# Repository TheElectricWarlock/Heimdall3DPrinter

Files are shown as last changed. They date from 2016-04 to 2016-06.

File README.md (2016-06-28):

# Heimdall3DPrinter
The Heimdall is a CoreXY 3D Printer capable of fast and reliable printing. It uses 1515 Aluminum extrusions for the enclosing frame. 

For more information regarding the printer visit the project's wiki.

## Changelog

### Version 1.3

-Improvements in XY stepper motor brackets for better stability.

### Version 1.2

-Added two new types of clips for better cable management that insert on the 1515 extrusions. 

### Version 1.1

-Added a new 1515 Extrusion to the back of the frame for mounting the power supply, Arduino Mega and Ramps.
-New Brackets for the power supply.
-New Bracket for the Arduino Mega and Ramps board. 
-Changes in bill of materials. 

## Things To Change

-Z Axis and Bed brackets for smoother Z axis movements, bed leveling and stability.

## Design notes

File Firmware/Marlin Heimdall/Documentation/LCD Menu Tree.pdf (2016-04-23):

# Marlin LCD Menu Tree

Main Menu | Tune Menu | Move Menu
Info screen | Main | Prepare
Tune | Speed | Move 10mm | Move Menu
Prepare | Nozzle | Move 1mm | Move axis
Control | Nozzle2 | Move 0.1mm | Move X
Pause print | Nozzle3 | | Move Y
Resume print | Bed | | Move Z
Stop print | Fan speed | Temperature Menu | Extruder
Print from SD | Flow | Control
Change SD card | Babystep X | Nozzle
No SD card | Babystep Y | Nozzle2
Init. SD card | Babystep Z | Nozzle3
| Change filament | Bed
| | Fan speed
| | Autotemp
| Prepare Menu | \002 Min
| Main | \002 Max | Preheat PLA
| Autostart | \002 Fact | Temperature
| Disable steppers | PID-P | Fan speed
| Auto home | PID-I | Nozzle
| Preheat PLA | PID-D | Bed
| Preheat ABS | PID-C | Store memory
| Cooldown | Preheat PLA conf
| Switch power off | Preheat ABS conf | Preheat ABS
Switch power on | Temperature
Move axis | Fan speed
| Motion Menu | Nozzle
| Control | Bed
Control Menu | Z Offset | Store memory
Main | Accel
Temperature | Vxy-jerk
Motion | Vz-jerk
LCD contrast | Ve-jerk
Retract | Vmax x
Store memory | Vmax y
Load memory | Vmax z
Restore failsafe | Vmax e
| Vmin
| VTrav min
SD Card Menu | Amax x
Main | Amax y
Refresh | Amax z
filenames | Amax e
| A-retract
| Xsteps/mm
| Ysteps/mm
| Zsteps/mm
| Esteps/mm
| Endstop abort

Retract Menu
Control
AutoRetr.
Retract mm
Retract F
Hop mm
UnRet +mm
UnRet F

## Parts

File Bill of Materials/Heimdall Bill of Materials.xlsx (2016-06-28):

Item # | Item Name | Amount | Source/Where to buy | Comment
Electronics
1 | Arduino Mega | 1 | Folgertech or Ebay. | Cheap Chinese copies should work well too.
2 | Ramps Shield | 1 | Folgertech or Ebay. | Cheap Chinese copies should work well too.
3 | Polulu Stepper Drivers | 4 | Folgertech or Ebay. | You can buy at least 1 more than the number shown here, just in case you fry one.
4 | Nema 17 Stepper Motors | 4 | Folgertech or Ebay. | The bigger the better, mostly for the Extruder.
5 | Makerbot Style Endstops | 3 | Folgertech or Ebay. | Simple endstops can be found anywhere.
6 | 360W 12V Power Supply | 1 | Folgertech or Ebay. | You can buy a lower watage one if not using a heated bed.
7 | Heated bed (200x200mm) | 1 | Folgertech or Ebay. | Optional, you can still use the printer without one. You get more printing area, but might not be able to print with abs.
8 | Hotend w/ Fan | 1 | E3D, Folgertech or Ebay. | You can buy your hotend wherever you want, as long as it is not too cheap and is similar to an E3D.
Mechanical Parts
9 | 5/16 - 18 Stainless Steel Threaded Rod (340mm) | 1 | Home Depot or any hardware store. | Z axis Threaded rod, if you want to use a Metric one, you can use a M8 Stainless Steel threaded rod.
10 | 5/16 - 18 Stainless Steel Nuts | 3 | Home Depot or any hardware store. | You only need one, more just in case. For Metric, you can use an M8 nut.
11 | 8mm Hardened Linear Rods X (260mm) | 2 | Folgertech or Ebay. | If the seller does not have this size, you might need to order a slightly longer one and cut it yourself.
12 | 8mm Hardened Linear Rods Y (390mm) | 2 | Folgertech or Ebay. | If the seller does not have this size, you might need to order a slightly longer one and cut it yourself.
13 | 8mm Hardened Linear Rods Z (400mm) | 2 | Folgertech or Ebay. | If the seller does not have this size, you might need to order a slightly longer one and cut it yourself.
14 | 1515 Aluminium Extrusions (400mm) | 4 | Misumi (USA) | Order them pre-cut from Misumi.
15 | 1515 Aluminium Extrusions (360mm) | 13 | Misumi (USA) | Order them pre-cut from Misumi.
16 | 5 Meters GT2 Timing Belt | 1 | Ebay. | If you can find these with the pulleys included, then it is way better.
17 | PTFE Tubing (Bowden Extruder) | 1 | Ebay, Amazon, | Make sure it is decent quality and for 1.75mm filament.
18 | PTFE Pushfit Connectors | 2 | Ebay, Amazon. | Mines are those M10 compatible pushfittings, they tend to come with hotends sometimes. These are compatible with the bowden extruder.
19 | GT2 Pulleys | 2 | Folgertech or Ebay. | Might come with the belts, if they do, there is no need to order more.
20 | Stiff M3 Screws Compatible Springs | 5 | Ebay or Hardware Store. | 4 for bed, 1 for bowden extruder.
21 | LM8LUU Linear Bearings | 6 | Folgertech or Ebay. | Linear Bearings For the Axis.
22 | 624Z Bearing | 1 | Ebay. | Bearing for the bowden extruder in the STL files.
23 | 625ZZ Bearings | 8 | Ebay. | Bearings for the XY axis.
24 | MK8 Style Pulley | 1 | Ebay. | Pulley for the bowden extruder. This one works well with the extruder in the STL files.
25 | MDF Board (250x250mm) | 1 | Home Depot or any hardware store. | For the base of the bed.
Fasteners
26 | M3 Screws | 224 | Hardware stores, Ebay, MCMaster-Carr | Too many to count, you can get long ones (about 40-50mm) and just cut them.
27 | M3 Nuts | 220 | Hardware stores, Ebay, MCMaster-Carr | You will need about the same amount or a little less as the M3 screws.
28 | M3 Washers | 120 | Hardware stores, Ebay, MCMaster-Carr | Washers to get good spacing between parts.
29 | M4 Screws (28mm) | 2 | Hardware stores, Ebay, MCMaster-Carr | Needed for the Y Carriage’s bearings. Buy more just in case.
30 | M4 Screws (16mm) | 1 | Hardware stores, Ebay, MCMaster-Carr | Needed for the Bowden Extruder.
31 | M4 Screws (20mm) | 1 | Hardware stores, Ebay, MCMaster-Carr | Needed for the Bowden Extruder.
32 | M4 Nuts | 4 | Hardware stores, Ebay, MCMaster-Carr | Needed for the Y Carriage’s bearings and Bowden Extruder. Buy more just in case.
33 | M5 Screws (24mm) | 8 | Hardware stores, Ebay, MCMaster-Carr | 4 for bed, as well as 4 for the corner bearing holders at the XY axis. Buy More to have around just in case.
34 | M5 Nuts | 8 | Hardware stores, Ebay, MCMaster-Carr | 4 for bed, as well as 4 for the corner bearing holders at the XY axis. Buy More to have around just in case.
35 | Small Zipties (or Cable Ties) | 8 | Hardware stores, Ebay, MCMaster-Carr | For the X and Y axis for attaching the linear bearings to attach to the 3D printed parts.
Miscelaneous Parts
36 | Piece of Window Glass (200x200mm) | 1 | Hardware stores, framing stores. | For the printing bed.
37 | Small Paper Clamps | 4 | Office Supply stores, 99c stores. | To hold the piece of glass to the bed. You might have some around. The smaller the better.
Optional Parts
38 | 2004 LCD Controller | 1 | Folgertech or Ebay. | Optional, if you want you can buy one, if not you can print from USB.
39 | SD Card (1-4GB) | 1 | Folgertech or Ebay. | For LCD display.
40 | 24" (24 Inches) 2004 & 12864 LCD Extension Cables | 1 | Folgertech. | Extension cables for the 2004 lcd
41 | 5mm to 8mm Flexible Coupling | 1 | Folgertech. | You can buy this if you dont want to 3D print a coupling. Tend to be more reliable than 3D printed ones.
42 | MDF Board (You choose the size) | 1 | Home Depot or any hardware store. | To mount the electronics to it. I tend to hide my electronics at the back with one of these.

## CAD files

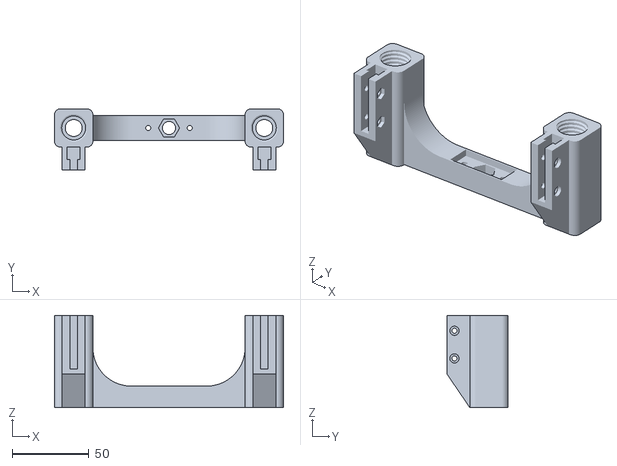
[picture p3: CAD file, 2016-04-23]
STL Files/Heimdall Bed Main Body - 1.stl
149.0 x 40.0 x 60.0

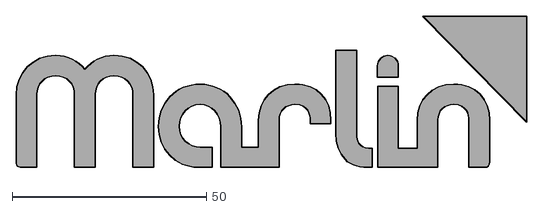
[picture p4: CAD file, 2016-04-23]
Firmware/Marlin Heimdall/Documentation/Logo/Marlin Logo.dxf
131.6 x 39.5

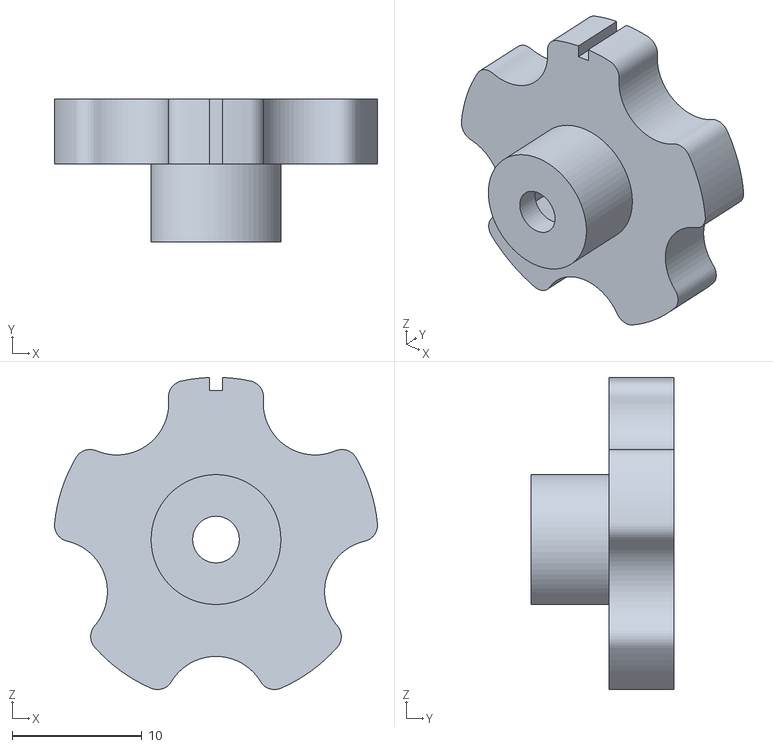
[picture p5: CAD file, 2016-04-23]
Optional STL Files/Bed Thumbwheels/Bed Thumbwheel Thingiverse:CaliRaisin - 4.stl
24.9 x 11.0 x 24.0

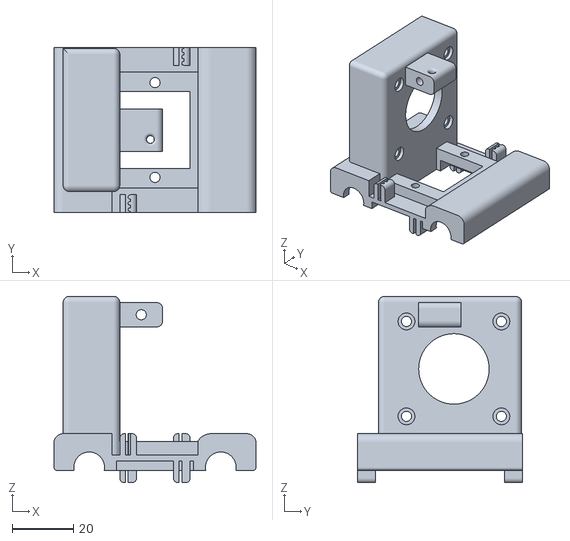
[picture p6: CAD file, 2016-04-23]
Optional STL Files/Direct Drive Extruder/Heimdall Direct Drive Extruder X Carriage - 1.stl
66.0 x 54.0 x 60.9

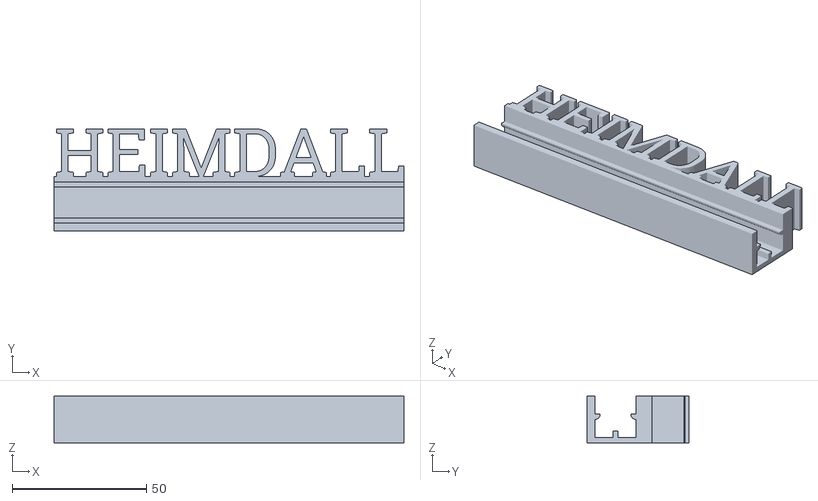
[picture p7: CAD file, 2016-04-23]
Optional STL Files/Heimdall Logo/Heimdall Logo - 1.stl
130.4 x 38.2 x 17.4

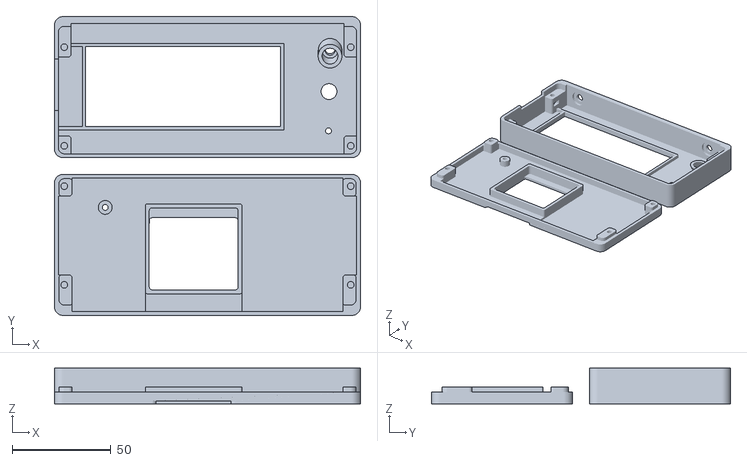
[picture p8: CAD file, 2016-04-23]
Optional STL Files/LCD/LCD Case Thingiverse:Kyo.stl
155.0 x 151.4 x 18.0

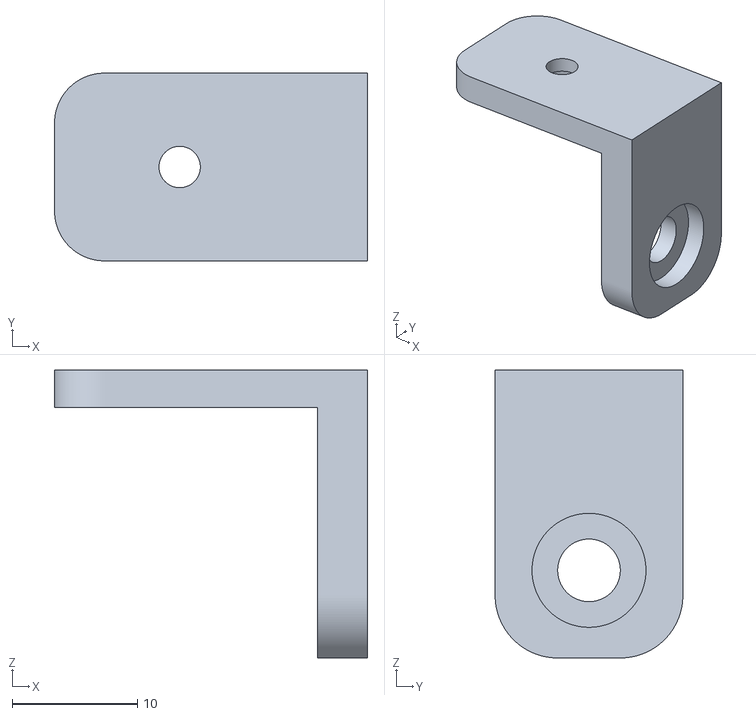
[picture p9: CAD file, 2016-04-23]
Optional STL Files/LED Strips/Heimdall Bracket for LEDS - 2.stl
25.0 x 15.0 x 23.0

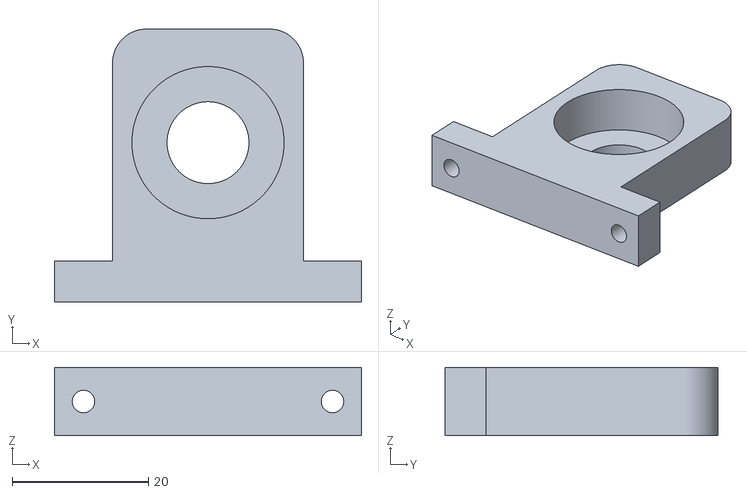
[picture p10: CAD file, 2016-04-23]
Optional STL Files/More Support/Heimdall Z Axis Threaded Rod Stabilizer - 1.stl
45.0 x 40.0 x 10.0

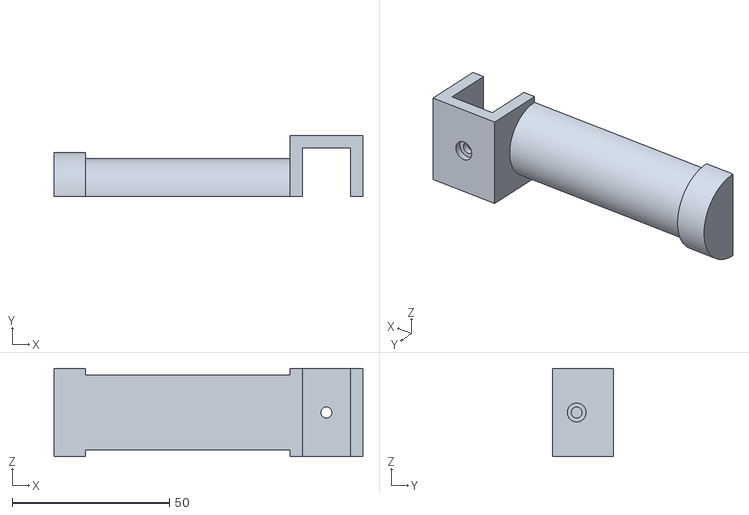
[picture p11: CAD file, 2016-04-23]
Optional STL Files/Spool Holder/Heimdall Spool Holder - 1.stl
98.3 x 19.3 x 28.0

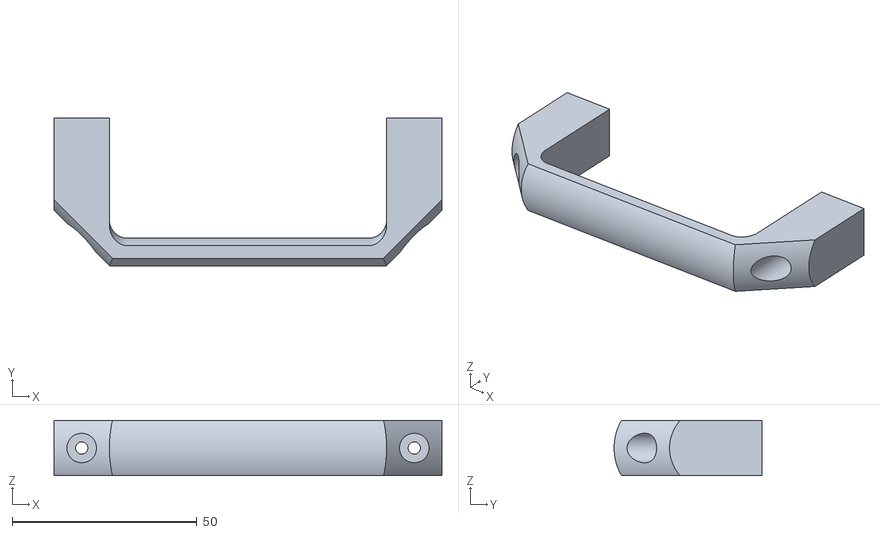
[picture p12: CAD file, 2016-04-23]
Optional STL Files/Top Handles/1515 Top Handles Thingiverse:thehans - 2.stl
105.0 x 40.0 x 15.0

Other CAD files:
CAD Files/Solidworks(.sldprt)/Heimdall Bed Main Body.sldprt
CAD Files/Solidworks(.sldprt)/Arduino Mega and Ramps Bracket.sldprt
CAD Files/Solidworks(.sldprt)/Optional CAD Files/Cable Management/Cable Management Clip 1.sldprt
CAD Files/Solidworks(.sldprt)/Optional CAD Files/Direct Drive Extruder/Heimdall Direct Drive Extruder X Carriage.sldprt
CAD Files/Solidworks(.sldprt)/Optional CAD Files/Heimdall Logo/Heimdall Logo.sldprt
CAD Files/Solidworks(.sldprt)/Optional CAD Files/LED Strips/Heimdall Fixture for LEDS.sldprt
CAD Files/Solidworks(.sldprt)/Optional CAD Files/More Support/Heimdall Z Axis Threaded Rod Stabilizer.sldprt
CAD Files/Solidworks(.sldprt)/Optional CAD Files/Spool Holder/Heimdall Spool Holder.sldprt
CAD Files/Parasolid(.x_t)/360W Power Supply Bracket.x_t
CAD Files/Parasolid(.x_t)/Arduino Mega and Ramps Bracket.x_t
CAD Files/Parasolid(.x_t)/Heimdall Bed Main Body.x_t
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

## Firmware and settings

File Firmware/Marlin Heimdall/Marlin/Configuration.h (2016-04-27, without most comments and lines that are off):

#define CONFIGURATION_H
#include "boards.h"
#define STRING_VERSION_CONFIG_H __DATE__ "12-19-15" __TIME__ // build date and time
#define STRING_CONFIG_H_AUTHOR "(none, default config)" // Who made the changes.
#define SERIAL_PORT 0
#define BAUDRATE 250000
  #define MOTHERBOARD 33
 #define CUSTOM_MENDEL_NAME "RepRap Heimdall"
#define EXTRUDERS 1
#define POWER_SUPPLY 1
#define TEMP_SENSOR_0 1
#define TEMP_SENSOR_1 1
#define TEMP_SENSOR_2 0
#define TEMP_SENSOR_BED 0
#define MAX_REDUNDANT_TEMP_SENSOR_DIFF 10
#define TEMP_RESIDENCY_TIME 10  // (seconds)
#define TEMP_HYSTERESIS 3       // (degC) range of +/- temperatures considered "close" to the target one
#define TEMP_WINDOW     1       // (degC) Window around target to start the residency timer x degC early.
#define HEATER_0_MINTEMP 5
#define HEATER_1_MINTEMP 5
#define HEATER_2_MINTEMP 5
#define BED_MINTEMP 5
#define HEATER_0_MAXTEMP 250
#define HEATER_1_MAXTEMP 250
#define HEATER_2_MAXTEMP 250
#define BED_MAXTEMP 150
#define PIDTEMP
#define BANG_MAX 255 // limits current to nozzle while in bang-bang mode; 255=full current
#define PID_MAX BANG_MAX // limits current to nozzle while PID is active (see PID_FUNCTIONAL_RANGE below); 255=full current
  #define PID_FUNCTIONAL_RANGE 10 // If the temperature difference between the target temperature and the actual temperature
  #define PID_INTEGRAL_DRIVE_MAX PID_MAX  //limit for the integral term
  #define K1 0.95 //smoothing factor within the PID
  #define PID_dT ((OVERSAMPLENR * 10.0)/(F_CPU / 64.0 / 256.0)) //sampling period of the temperature routine
    #define  DEFAULT_Kp 22.2
    #define  DEFAULT_Ki 1.08
    #define  DEFAULT_Kd 114
#define MAX_BED_POWER 255 // limits duty cycle to bed; 255=full current
#define PREVENT_DANGEROUS_EXTRUDE
#define PREVENT_LENGTHY_EXTRUDE
#define EXTRUDE_MINTEMP 170
#define EXTRUDE_MAXLENGTH (X_MAX_LENGTH+Y_MAX_LENGTH) //prevent extrusion of very large distances.
#define THERMAL_RUNAWAY_PROTECTION_PERIOD 40 //in seconds
#define THERMAL_RUNAWAY_PROTECTION_HYSTERESIS 10 // in degree Celsius
 #define COREXY
#define ENDSTOPPULLUPS // Comment this out (using // at the start of the line) to disable the endstop pullup resistors
  #define ENDSTOPPULLUP_XMAX
  #define ENDSTOPPULLUP_YMAX
  #define ENDSTOPPULLUP_ZMAX
  #define ENDSTOPPULLUP_XMIN
  #define ENDSTOPPULLUP_YMIN
  #define ENDSTOPPULLUP_ZMIN
const bool X_MIN_ENDSTOP_INVERTING = true; // set to true to invert the logic of the endstop.
const bool Y_MIN_ENDSTOP_INVERTING = true; // set to true to invert the logic of the endstop.
const bool Z_MIN_ENDSTOP_INVERTING = true; // set to true to invert the logic of the endstop.
const bool X_MAX_ENDSTOP_INVERTING = true; // set to true to invert the logic of the endstop.
const bool Y_MAX_ENDSTOP_INVERTING = true; // set to true to invert the logic of the endstop.
const bool Z_MAX_ENDSTOP_INVERTING = true; // set to true to invert the logic of the endstop.
#if defined(COREXY) && !defined(DISABLE_MAX_ENDSTOPS)
  #define DISABLE_MAX_ENDSTOPS
#endif
#define X_ENABLE_ON 0
#define Y_ENABLE_ON 0
#define Z_ENABLE_ON 0
#define E_ENABLE_ON 0 // For all extruders
#define DISABLE_X true
#define DISABLE_Y true
#define DISABLE_Z true
#define DISABLE_E false // For all extruders
#define DISABLE_INACTIVE_EXTRUDER true //disable only inactive extruders and keep active extruder enabled
#define INVERT_X_DIR false    // for Mendel set to false, for Orca set to true
#define INVERT_Y_DIR false    // for Mendel set to true, for Orca set to false
#define INVERT_Z_DIR false     // for Mendel set to false, for Orca set to true
#define INVERT_E0_DIR false   // for direct drive extruder v9 set to true, for geared extruder set to false
#define INVERT_E1_DIR false    // for direct drive extruder v9 set to true, for geared extruder set to false
#define INVERT_E2_DIR false   // for direct drive extruder v9 set to true, for geared extruder set to false
#define X_HOME_DIR -1
#define Y_HOME_DIR -1
#define Z_HOME_DIR -1
#define min_software_endstops false // If true, axis won't move to coordinates less than HOME_POS.
#define max_software_endstops true  // If true, axis won't move to coordinates greater than the defined lengths below.
#define X_MAX_POS 180
#define X_MIN_POS 0
#define Y_MAX_POS 220
#define Y_MIN_POS 0
#define Z_MAX_POS 230
#define Z_MIN_POS 0
#define X_MAX_LENGTH (X_MAX_POS - X_MIN_POS)
#define Y_MAX_LENGTH (Y_MAX_POS - Y_MIN_POS)
#define Z_MAX_LENGTH (Z_MAX_POS - Z_MIN_POS)
#define MANUAL_X_HOME_POS 0
#define MANUAL_Y_HOME_POS 0
#define MANUAL_Z_HOME_POS 0
#define NUM_AXIS 4 // The axis order in all axis related arrays is X, Y, Z, E
#define HOMING_FEEDRATE {80*60, 80*60, 5.5*60, 0}  // set the homing speeds (mm/min)
#define DEFAULT_AXIS_STEPS_PER_UNIT   {80.00, 80.00 ,2267.72 ,100}
#define DEFAULT_MAX_FEEDRATE          {500, 500, 5, 25}    // (mm/sec)
#define DEFAULT_MAX_ACCELERATION      {9000,9000,100,10000}    // X, Y, Z, E maximum start speed for accelerated moves. E default values are good for Skeinforge 40+, for older versions raise them a lot.
#define DEFAULT_ACCELERATION          3000    // X, Y, Z and E max acceleration in mm/s^2 for printing moves
#define DEFAULT_RETRACT_ACCELERATION  3000   // X, Y, Z and E max acceleration in mm/s^2 for retracts
#define DEFAULT_XYJERK                20.0    // (mm/sec)
#define DEFAULT_ZJERK                 0.4     // (mm/sec)
#define DEFAULT_EJERK                 5.0    // (mm/sec)
#define CUSTOM_M_CODES
  #define CUSTOM_M_CODE_SET_Z_PROBE_OFFSET 851
  #define Z_PROBE_OFFSET_RANGE_MIN -15
  #define Z_PROBE_OFFSET_RANGE_MAX -5
#define PLA_PREHEAT_HOTEND_TEMP 180
#define PLA_PREHEAT_HPB_TEMP 70
#define PLA_PREHEAT_FAN_SPEED 255   // Insert Value between 0 and 255
#define ABS_PREHEAT_HOTEND_TEMP 240
#define ABS_PREHEAT_HPB_TEMP 100
#define ABS_PREHEAT_FAN_SPEED 255   // Insert Value between 0 and 255
#define SOFT_PWM_SCALE 0
#define FILAMENT_SENSOR_EXTRUDER_NUM	0  //The number of the extruder that has the filament sensor (0,1,2)
#define MEASUREMENT_DELAY_CM			14  //measurement delay in cm.  This is the distance from filament sensor to middle of barrel
#define DEFAULT_NOMINAL_FILAMENT_DIA  3.0  //Enter the diameter (in mm) of the filament generally used (3.0 mm or 1.75 mm) - this is then used in the slicer software.  Used for sensor reading validation
#define MEASURED_UPPER_LIMIT          3.30  //upper limit factor used for sensor reading validation in mm
#define MEASURED_LOWER_LIMIT          1.90  //lower limit factor for sensor reading validation in mm
#define MAX_MEASUREMENT_DELAY			20  //delay buffer size in bytes (1 byte = 1cm)- limits maximum measurement delay allowable (must be larger than MEASUREMENT_DELAY_CM  and lower number saves RAM)
#define DEFAULT_MEASURED_FILAMENT_DIA  DEFAULT_NOMINAL_FILAMENT_DIA  //set measured to nominal initially
#include "Configuration_adv.h"
#include "thermistortables.h"

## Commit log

2016-04-23 Fist commit, all folders and files necessary to make the 3D printer.
    [1515 Top Handles Thingiverse:thehans - 2.stl, 3D+printer+bed+v3+-+main+body.3dm, 3D+printer+bed+v3+-+main+body.sldprt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]
2016-04-23 Added all the CAD files to their respective folders
    [1515 Top Handles Thingiverse:thehans - 2.stl, Bed Thumbwheel Thingiverse:CaliRaisin - 4.stl, Heimdall Bed Main Body.3dm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]
2016-04-23 Moving some files and adding CAD Designs
    [1515 Top Handles Thingiverse:thehans - 2.stl, Bed Thumbwheel Thingiverse:CaliRaisin - 4.stl, Heimdall Bracket for LEDS - 2.stl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]
2016-04-24 Completed the bill of materials
    [Heimdall Bill of Materials(Incomplete).xlsx, Heimdall Bill of Materials.xlsx]
2016-04-24 Some changes to the bill of materials
    [Heimdall Bill of Materials.xlsx]
2016-04-27 Changed the number of endstop holders needed
    [Endstop Holder Thingiverse:Caracol_affairs - 2.stl]
2016-04-27 Changes in the Readme file as well as the Firmware
    [Configuration.h]
2016-06-28 Changes to many of the 3D printer's parts and documentation
    [360W Power Supply Bracket - 2.stl, 360W Power Supply Bracket.3dm, 360W Power Supply Bracket.sldprt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]
